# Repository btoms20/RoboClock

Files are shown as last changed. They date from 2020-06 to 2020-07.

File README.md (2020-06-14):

# RoboClock

Turning the [EEZYbotARM](https://www.thingiverse.com/thing:1015238) into a time telling machine! 

RoboClock_Timelapse

### Overview
This project attempts to use the [EEZYbotARM](https://www.thingiverse.com/thing:1015238) designed by [daGHIZmo](https://www.thingiverse.com/daGHIZmo) ([Original License](https://creativecommons.org/licenses/by-nc/4.0/legalcode)) to keep time by arranging a set of 3D printed numbers in the correct order.

The clock consists of three parts...
*  A Podium
    *  A stand that supports the digits used to tell the current time
*  An Inventory
    *  A chainlink / sprocket / tray system that stores all of the excess digits
    *  See Inventory.h for the arduino code
    *  See /Parts/Inventory for parts (stl) or [Thingiverse](https://www.thingiverse.com/thing:4457850/files)
*  The EEZYbot Robot Arm (see Arm.h)
    *  Responsible for moving the physical digits between the inventory and podium
    *  See Arm.h for the arduino code
    *  See [Thingiverse](https://www.thingiverse.com/thing:1015238) for parts
    *  With modified gripper assembly at 
       *  /Parts/GripperModified
       *  or [Thingiverse](https://www.thingiverse.com/thing:4457850)

Every 5 minutes the arm rearranges/replaces the numbers on the podium to reflect the current time. Depending on how many numbers need changing, the entire update cycle can last anywhere from 45 to 90 secs.

### How To
Check out the [instructables for a detailed guide](https://www.instructables.com/id/RoboClock/) to building your own
*  Download, Slice, Print and Assemble the [EEZYbotARM](https://www.thingiverse.com/thing:1015238) 
*  Download, Slice, Print and Assemble the [RoboClock](https://www.thingiverse.com/thing:4457850) parts
*  Pro Tip 💡: Before printing the entire 18 segment chain, print a few segments of the chain and adjust the height of Chain_Spacer.stl to make sure your chain has the desired tolerances. It should rotate freely with minimal lateral sag.
*  Mount parts to surface
*  Upload the meastro_settings.txt to the Micro Maestro using the Maestro software from Pololu
*  Tweak the sequences if needed to ensure the pre-programmed sequences move the to the correct locations
*  Wire up the electronics / circuit
*  Download the arduino sketch and dependencies using the IDE's library manager
*  Enter your wifi's credentials in arduino_secrets.h (if using the MKR1000 Wifi)
*  Compile & Upload the code to the arduino
*  Arrange the numbers on the chain in the anti-clockwise order (0,0,1,1,1,2,2,3,3,4,4,5,5,5,6,7,8,9)
*  Place the remaining zero on the last podium slot ( _ , _ , _ , 0 ) 
*  Plug in and watch it probably not work...
*  Tune the maestro sequences until things work 

### Arduino SketchBooks
*  [RoboClock_Seeeduino](https://gitlab.com/btoms20/robotclock/-/tree/master/clock_seeeduino) (Tested and working)
    *  Includes 3 custom libraries
        *  Clock.h
            *  Main orchestrator between Inventory and Arm
            *  Responsible for determining operations to acheive a certain clock state
            *  Repsonsible for the synchronous execution of those operations to achive the desired clock state
        * Arm.h
            *  Responsible for running pre-recorded subroutines on the Micro Maestro
        * Inventory.h
            *  Responsible for presenting requested digits (or empty slots) via the stepper motor diver.
            *  Responsible for maintaining an inventory state (what digit resides in each slot).
*  [RoboClock_MKR1000](https://gitlab.com/btoms20/robotclock/-/tree/master/clock_mkr1000) (Tested and working)
    *  Uses the Arduino MKR1000 Wifi
    *  The same Clock, Arm and Inventory libraries as above with the addition of networked time sync via NTP
    *  Also includes a few simple functions to convert UTC to your timezone (while protecting for daylight savings time when appropriate) (not fully tested)
    *  Two operation modes (set the ```Inventory.usingSensors``` bool flag appropriately)
        *  Using Hall Effect Chain Sensors (closes the inventory loop to create a much more robust inventory system)
        *  Not using Chain Sensors (the chain system may bind and cause the stepper motor to lose steps, at which point the system can't recover)

### Arduino Libraries / Dependencies
*  [PololuMaestro](https://github.com/pololu/maestro-arduino)
*  [CheapStepper](https://github.com/tyhenry/CheapStepper)
*  Seeeduino Specific
    *  [Time & TimeLib](https://github.com/PaulStoffregen)
*  MKR1000 Specific
    *  [RTCZero](https://github.com/arduino-libraries/RTCZero/blob/master/src/RTCZero.h)

### Hardware ( ~150 USD if you need to purchase everything listed )
*  Pololu Servo Controller ([Micro Maestro](https://www.pololu.com/product/1350)) (requires 5v serial)
*  4x MG90S Servos
*  28BYJ-48 5V DC Stepper Motor 
*  ULN2003A Stepper Driver
*  MKR1000 or Seeeduino rev2.21 (used for its 5v gpio pins)
*  Voltage Level Shifter (if using 3.3v board like the Arduino MKR1000 Wifi)
*  5v ~3 Amp Power Supply
*  608ZZ Bearing
*  Assorted M3-M5 Nuts and Bolts (lock nuts recommended)
*  Jumper Wires and Breadboard
*  3x1mm Magnets
*  A3144 Hall Effect Sensors (optional but recommended)

### Tools
*  3D Printer
*  Windows Comp with USB for Pololu Meastro Software 
*  Arduino IDE
*  M3-M5 Allen Keys
*  Pliers
*  Wood Screws and Screw Driver
*  A surface to mount everything to (a recycled bookshelf works well)
*  Superglue
If using the chain sensor
*  Soldering Iron
*  2x Capacitors (0.1 uF)
*  2x Resistors (10k Ohms)

### Electronics / Circuit Diagram
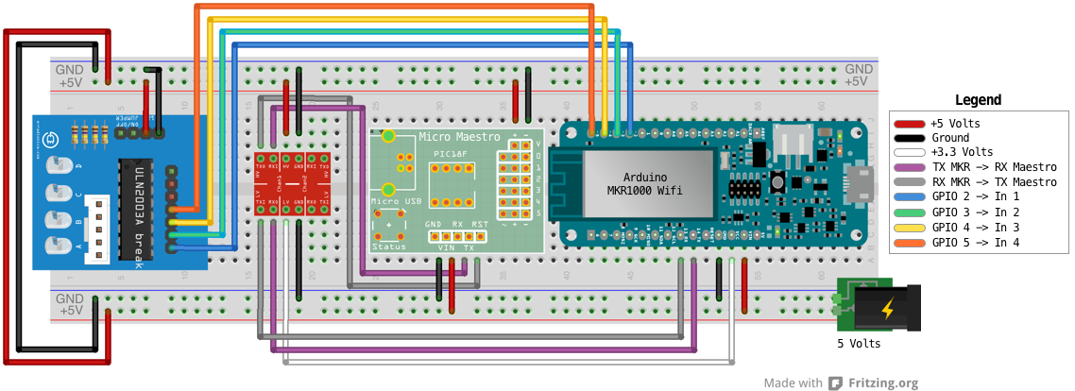
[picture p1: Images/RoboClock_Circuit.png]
RoboClock_Circuit


### Variants
* [x]  Seeeduino Controller (done)
    *  Pros:
        *  Makes development simple. Has 5v serial that makes interfacing with the micro maestro easy.
    *  Downsides 
        * No network for time sync / management 
        * Limited RAM (we're currently at ~85% memory and getting warnings on the Arduino IDE)
* [x]  Arduino MKR1000 (~~waiting for logic level shifter~~)
    *  Pros:
        *  Wifi built in for time sync / management
        *  Faster & more RAM
    *  Cons:
        *  3.3v architecture requires the use of a 3.3v <-> 5v Logic Level Shifter for communication with the Micro Maestro
* [ ]  TODO: Raspberry Pi Zero W (not started, 3.3v gpio as well)

### Notes & References
*  Arduino 
    * [Writing a Library](https://www.arduino.cc/en/Hacking/LibraryTutorial)  
*  MKR1000
    *  [Additional Serial Ports - Example Code](https://github.com/guywithaview/Arduino-Test/blob/master/sercom/sercom.ino)
    *  [Additional Serial Ports - Forum](https://forum.arduino.cc/index.php?topic=393296.0)
    *  [WiFiRTC Example](https://www.arduino.cc/en/Tutorial/WiFiRTC)
*  [Micro Maestro Documentation](https://www.pololu.com/product/1350)
*  [Unipolar -> Bipolar 28BYJ Conversion](https://coeleveld.com/wp-content/uploads/2016/10/Modifying-a-28BYJ-48-step-motor-from-unipolar-to-bipolar.pdf)
*  Raspberry Pi
    *  [28BYJ Stepper Motor & ULN2003 Driver](https://learn.adafruit.com/adafruits-raspberry-pi-lesson-10-stepper-motors/overview)  

### 3D Printed Parts
*  [EEZYbotARM MRK 1](https://www.thingiverse.com/thing:1015238) designed by [daGHIZmo](https://www.thingiverse.com/daGHIZmo) ([Original License](https://creativecommons.org/licenses/by-nc/4.0/legalcode))
*  [RoboClock](https://www.thingiverse.com/thing:4457850)

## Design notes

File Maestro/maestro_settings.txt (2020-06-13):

<!--Pololu Maestro servo controller settings file, http://www.pololu.com/catalog/product/1350-->
<UscSettings version="1">
  <NeverSuspend>false</NeverSuspend>
  <SerialMode>UART_FIXED_BAUD_RATE</SerialMode>
  <FixedBaudRate>9600</FixedBaudRate>
  <SerialTimeout>0</SerialTimeout>
  <EnableCrc>false</EnableCrc>
  <SerialDeviceNumber>12</SerialDeviceNumber>
  <SerialMiniSscOffset>0</SerialMiniSscOffset>
  <Channels ServosAvailable="6" ServoPeriod="156">
    <!--Period = 19.968 ms-->
    <!--Channel 0-->
    <Channel name="" mode="Servo" min="1792" max="10432" homemode="Off" home="1792" speed="0" acceleration="4" neutral="6000" range="1905" />
    <!--Channel 1-->
    <Channel name="" mode="Servo" min="3968" max="8000" homemode="Off" home="3968" speed="0" acceleration="0" neutral="6000" range="1905" />
    <!--Channel 2-->
    <Channel name="" mode="Servo" min="4032" max="9216" homemode="Off" home="4032" speed="0" acceleration="8" neutral="6000" range="1905" />
    <!--Channel 3-->
    <Channel name="" mode="Servo" min="3584" max="8000" homemode="Off" home="3584" speed="0" acceleration="8" neutral="6000" range="1905" />
    <!--Channel 4-->
    <Channel name="" mode="Servo" min="1600" max="9984" homemode="Off" home="1600" speed="0" acceleration="0" neutral="6000" range="1905" />
    <!--Channel 5-->
    <Channel name="" mode="Servo" min="5824" max="9216" homemode="Off" home="5824" speed="0" acceleration="10" neutral="6400" range="1905" />
  </Channels>
  <Sequences>
    <Sequence name="ActiveHome">
      <Frame name="ActiveHome" duration="2000">5920 0 6800 4000 0 5824</Frame>
    </Sequence>
    <Sequence name="Pick0">
      <Frame name="Home" duration="1500">5920 0 6800 4000 0 5824</Frame>
      <Frame name="Frame 0" duration="2500">9800 0 6800 4000 0 8000</Frame>
      <Frame name="Frame 1" duration="1000">9800 0 6160 4600 0 8000</Frame>
      <Frame name="Frame 2" duration="1500">9800 0 4800 5600 0 8000</Frame>
      <Frame name="Frame 3" duration="1000">9800 0 4800 5600 0 5824</Frame>
      <Frame name="Frame 4" duration="200">9600 0 4800 5600 0 5824</Frame>
      <Frame name="Frame 5" duration="1500">9600 0 6800 4000 0 5824</Frame>
      <Frame name="Home" duration="1500">5920 0 6800 4000 0 5824</Frame>
    </Sequence>
    <Sequence name="Pick1">
      <Frame name="Home" duration="1500">5920 0 6800 4000 0 5824</Frame>
      <Frame name="Frame 0" duration="2500">9800 0 6800 4000 0 8000</Frame>
      <Frame name="Frame 1" duration="1000">9800 0 6160 5280 0 8000</Frame>
      <Frame name="Frame 2" duration="1000">9800 0 5200 6000 0 8000</Frame>
      <Frame name="Frame 3" duration="1000">9800 0 5200 6000 0 5824</Frame>
      <Frame name="Frame 4" duration="200">9600 0 5200 6000 0 5824</Frame>
      <Frame name="Frame 5" duration="1500">9600 0 6160 5280 0 5824</Frame>
      <Frame name="Frame 6" duration="1500">9600 0 6800 4000 0 5824</Frame>
      <Frame name="Home" duration="1500">5920 0 6800 4000 0 5824</Frame>
    </Sequence>
    <Sequence name="Pick2">
      <Frame name="Home" duration="1500">5920 0 6800 4000 0 5824</Frame>
      <Frame name="Frame 0" duration="2500">9800 0 6800 4000 0 8000</Frame>
      <Frame name="Frame 1" duration="1000">9800 0 6800 5880 0 8000</Frame>
      <Frame name="Frame 2" duration="1000">9800 0 5720 6520 0 8000</Frame>
      <Frame name="Frame 3" duration="1000">9800 0 5720 6520 0 5824</Frame>
      <Frame name="Frame 4" duration="200">9600 0 5720 6520 0 5824</Frame>
      <Frame name="Frame 5" duration="1500">9600 0 6800 5880 0 5824</Frame>
      <Frame name="Frame 6" duration="1500">9600 0 6800 4000 0 5824</Frame>
      <Frame name="Home" duration="1500">5920 0 6800 4000 0 5824</Frame>
    </Sequence>
    <Sequence name="Pick3">
      <Frame name="Home" duration="1500">5920 0 6800 4000 0 5824</Frame>
      <Frame name="Frame 0" duration="2500">9800 0 6800 4000 0 8000</Frame>
      <Frame name="Frame 1" duration="1000">9800 0 7200 6800 0 8000</Frame>
      <Frame name="Frame 2" duration="1000">9800 0 6320 7120 0 8000</Frame>
      <Frame name="Frame 3" duration="1000">9800 0 6320 7120 0 5824</Frame>
      <Frame name="Frame 4" duration="200">9680 0 6320 7120 0 5824</Frame>
      <Frame name="Frame 5" duration="1500">9680 0 7600 6800 0 5824</Frame>
      <Frame name="Frame 6" duration="1500">9680 0 6800 4000 0 5824</Frame>
      <Frame name="Home" duration="1500">5920 0 6800 4000 0 5824</Frame>
    </Sequence>
    <Sequence name="PickTray">
      <Frame name="Home" duration="1500">5920 0 6800 4000 0 5824</Frame>
      <Frame name="Frame 0" duration="2500">2200 0 6800 4000 0 8000</Frame>
      <Frame name="Frame 2" duration="1500">2200 0 5400 5400 0 8000</Frame>
      <Frame name="Frame 3" duration="1000">2200 0 5400 5400 0 5824</Frame>
      <Frame name="Frame 5" duration="1">2600 0 5400 5400 0 5824</Frame>
      <Frame name="Frame 4" duration="2000">2600 0 6800 4000 0 5824</Frame>
      <Frame name="Home" duration="1500">5920 0 6800 4000 0 5824</Frame>
    </Sequence>
    <Sequence name="Place0">
      <Frame name="Home" duration="1500">5920 0 6800 4000 0 5824</Frame>
      <Frame name="Frame 0" duration="2500">9800 0 6800 4000 0 5824</Frame>
      <Frame name="Frame 1" duration="1000">9800 0 6160 4600 0 5824</Frame>
      <Frame name="Frame 2" duration="1500">9800 0 4800 5600 0 5824</Frame>
      <Frame name="Frame 3" duration="750">9800 0 4800 5600 0 8000</Frame>
      <Frame name="Frame 4" duration="1500">9800 0 6800 4000 0 8000</Frame>
      <Frame name="Frame 5" duration="750">9800 0 6800 4000 0 6000</Frame>
      <Frame name="Home" duration="1500">5920 0 6800 4000 0 5824</Frame>
    </Sequence>
    <Sequence name="Place1">
      <Frame name="Home" duration="1500">5920 0 6800 4000 0 5824</Frame>
      <Frame name="Frame 0" duration="2500">9840 0 6800 4000 0 5824</Frame>
      <Frame name="Frame 1" duration="1500">9840 0 6400 5280 0 5824</Frame>
      <Frame name="Frame 2" duration="1500">9840 0 5200 6000 0 5824</Frame>
      <Frame name="Frame 3" duration="750">9840 0 5200 6000 0 8000</Frame>
      <Frame name="Frame 4" duration="1500">9840 0 6160 5280 0 8000</Frame>
      <Frame name="Frame 5" duration="1000">9840 0 6800 4000 0 6000</Frame>
      <Frame name="Home" duration="1500">5920 0 6800 4000 0 5824</Frame>
    </Sequence>
    <Sequence name="Place2">
      <Frame name="Home" duration="1500">5920 0 6800 4000 0 5824</Frame>
      <Frame name="Frame 0" duration="2500">9880 0 6800 4000 0 5824</Frame>
      <Frame name="Frame 1" duration="1000">9880 0 6800 5880 0 5824</Frame>
      <Frame name="Frame 6" duration="1000">9880 0 6000 6120 0 5824</Frame>
      <Frame name="Frame 2" duration="1000">9880 0 5720 6520 0 5824</Frame>
      <Frame name="Frame 3" duration="750">9880 0 5720 6520 0 8000</Frame>
      <Frame name="Frame 4" duration="1000">9880 0 6800 5880 0 8000</Frame>
      <Frame name="Frame 5" duration="1000">9880 0 6800 4000 0 6000</Frame>
      <Frame name="Home" duration="1500">5920 0 6800 4000 0 5824</Frame>
    </Sequence>
    <Sequence name="Place3">
      <Frame name="Home" duration="1500">5920 0 6800 4000 0 5824</Frame>
      <Frame name="Frame 0" duration="2500">9880 0 6800 4000 0 5824</Frame>
      <Frame name="Frame 1" duration="1500">9880 0 7200 6800 0 5824</Frame>
      <Frame name="Frame 2" duration="1000">9880 0 6320 7040 0 5824</Frame>
      <Frame name="Frame 3" duration="750">9880 0 6600 7200 0 8000</Frame>
      <Frame name="Frame 4" duration="1000">9880 0 7200 6800 0 8000</Frame>
      <Frame name="Frame 5" duration="2000">9880 0 6800 4000 0 6000</Frame>
      <Frame name="Home" duration="1500">5920 0 6800 4000 0 5824</Frame>
    </Sequence>
    <Sequence name="PlaceTray">
      <Frame name="Home" duration="1500">5920 0 6800 4000 0 5824</Frame>
      <Frame name="Frame 0" duration="2500">2200 0 6800 4000 0 5824</Frame>
      <Frame name="Hover" duration="1500">2200 0 5800 5000 0 5824</Frame>
      <Frame name="Place" duration="1500">2200 0 5200 5400 0 6400</Frame>
      <Frame name="Frame 2" duration="750">2200 0 5200 5400 0 8000</Frame>
      <Frame name="Frame 3" duration="1500">2200 0 6800 4000 0 8000</Frame>
      <Frame name="Frame 4" duration="750">2200 0 6800 4000 0 6000</Frame>
      <Frame name="Home" duration="1500">5920 0 6800 4000 0 5824</Frame>
    </Sequence>
  </Sequences>
  <Script ScriptDone="true">begin
repeat

### Sequence subroutines: ###

# ActiveHome
sub ActiveHome
  2000 5920 0 6800 4000 0 6000 frame_0..5 # ActiveHome
  return
# Pick0
sub Pick0
  2500 9800 0 6800 4000 0 8000 frame_0..5 # Frame 0
  1000 6160 4600 frame_2_3 # Frame 1
  1500 4800 5600 frame_2_3 # Frame 2
  1000 5824 frame_5 # Frame 3
  200 9600 frame_0 # Frame 4
  1500 6800 4000 frame_2_3 # Frame 5
  return
# Pick1
sub Pick1
  2500 9800 0 6800 4000 0 8000 frame_0..5 # Frame 0
  1000 6160 5280 frame_2_3 # Frame 1
  1000 5200 6000 frame_2_3 # Frame 2
  1000 5824 frame_5 # Frame 3
  200 9600 frame_0 # Frame 4
  1500 6160 5280 frame_2_3 # Frame 5
  1500 6800 4000 frame_2_3 # Frame 6
  return
# Pick2
sub Pick2
  2500 9800 0 6800 4000 0 8000 frame_0..5 # Frame 0
  1000 5880 frame_3 # Frame 1
  1000 5720 6520 frame_2_3 # Frame 2
  1000 5824 frame_5 # Frame 3
  200 9600 frame_0 # Frame 4
  1500 6800 5880 frame_2_3 # Frame 5
  1500 4000 frame_3 # Frame 6
  return
# Pick3
sub Pick3
  2500 9800 0 6800 4000 0 8000 frame_0..5 # Frame 0
  1000 7200 6800 frame_2_3 # Frame 1
  1000 6320 7120 frame_2_3 # Frame 2
  1000 5824 frame_5 # Frame 3
  200 9680 frame_0 # Frame 4
  1500 7600 6800 frame_2_3 # Frame 5
  1500 6800 4000 frame_2_3 # Frame 6
  return
# PickTray
sub PickTray
  2500 2200 0 6800 4000 0 8000 frame_0..5 # Frame 0
  1500 5400 5400 frame_2_3 # Frame 2
  1000 5824 frame_5 # Frame 3
  1 2600 frame_0 # Frame 5
  2000 6800 4000 frame_2_3 # Frame 4
  return
# Place0
sub Place0
  2500 9800 0 6800 4000 0 5824 frame_0..5 # Frame 0
  1000 6160 4600 frame_2_3 # Frame 1
  1500 4800 5600 frame_2_3 # Frame 2
  750 8000 frame_5 # Frame 3
  1500 6800 4000 frame_2_3 # Frame 4
  750 6000 frame_5 # Frame 5
  return
# Place1
sub Place1
  2500 9840 0 6800 4000 0 5824 frame_0..5 # Frame 0
  1500 6400 5280 frame_2_3 # Frame 1
  1500 5200 6000 frame_2_3 # Frame 2
  750 8000 frame_5 # Frame 3
  1500 6160 5280 frame_2_3 # Frame 4
  1000 6800 4000 6000 frame_2_3_5 # Frame 5
  return
# Place2
sub Place2
  2500 9880 0 6800 4000 0 5824 frame_0..5 # Frame 0
  1000 5880 frame_3 # Frame 1
  1000 6000 6120 frame_2_3 # Frame 6
  1000 5720 6520 frame_2_3 # Frame 2
  750 8000 frame_5 # Frame 3
  1000 6800 5880 frame_2_3 # Frame 4
  1000 4000 6000 frame_3_5 # Frame 5
  return
# Place3
sub Place3
  2500 9880 0 6800 4000 0 5824 frame_0..5 # Frame 0
  1500 7200 6800 frame_2_3 # Frame 1
  1000 6320 7040 frame_2_3 # Frame 2
  750 6600 7200 8000 frame_2_3_5 # Frame 3
  1000 7200 6800 frame_2_3 # Frame 4
  2000 6800 4000 6000 frame_2_3_5 # Frame 5
  return
# PlaceTray
sub PlaceTray
  2500 2200 0 6800 4000 0 5824 frame_0..5 # Frame 0
  1500 5800 5000 frame_2_3 # Hover
  1500 5200 5400 6400 frame_2_3_5 # Place
  750 8000 frame_5 # Frame 2
  1500 6800 4000 frame_2_3 # Frame 3
  750 6000 frame_5 # Frame 4
  return

sub frame_0..5
  5 servo
  4 servo
  3 servo
  2 servo
  1 servo
  0 servo
  delay
  return

sub frame_2_3
  3 servo
  2 servo
  delay
  return

sub frame_5
  5 servo
  delay
  return

sub frame_0
  0 servo
  delay
  return

sub frame_3
  3 servo
  delay
  return

sub frame_2_3_5
  5 servo
  3 servo
  2 servo
  delay
  return

sub frame_3_5
  5 servo
  3 servo
  delay
  return
</Script>
</UscSettings>

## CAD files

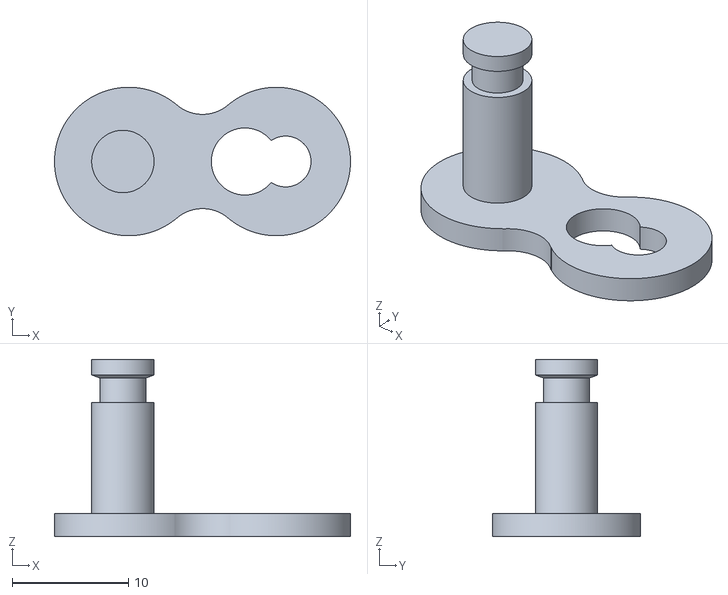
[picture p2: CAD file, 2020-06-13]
Parts/Inventory/Chain/Main_Bracket.stl
25.5 x 12.8 x 15.2

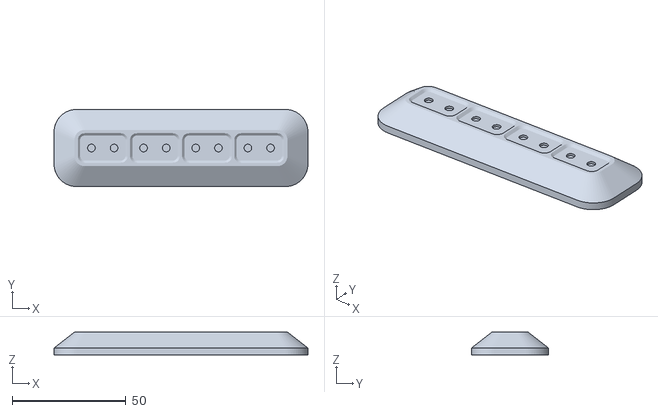
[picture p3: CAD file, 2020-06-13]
Parts/Clock_Podium.stl
111.9 x 34.0 x 10.0

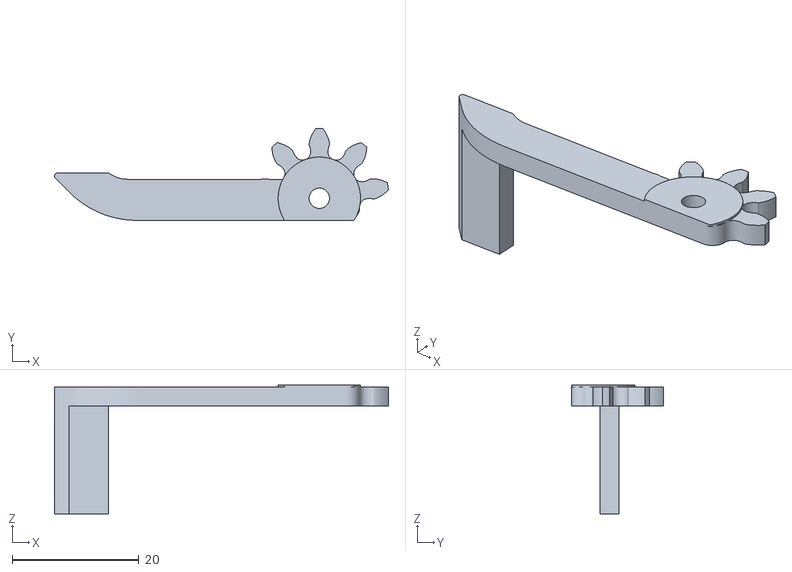
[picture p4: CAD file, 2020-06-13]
Parts/GripperModified/EBA_Left_Finger_Extended.stl
52.7 x 14.5 x 20.3

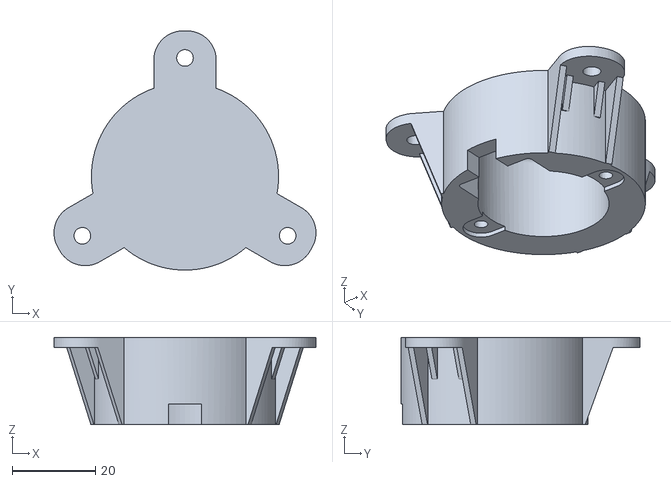
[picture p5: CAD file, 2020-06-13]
Parts/Inventory/28BYJ_Motor_Mount.stl
63.0 x 57.5 x 21.0

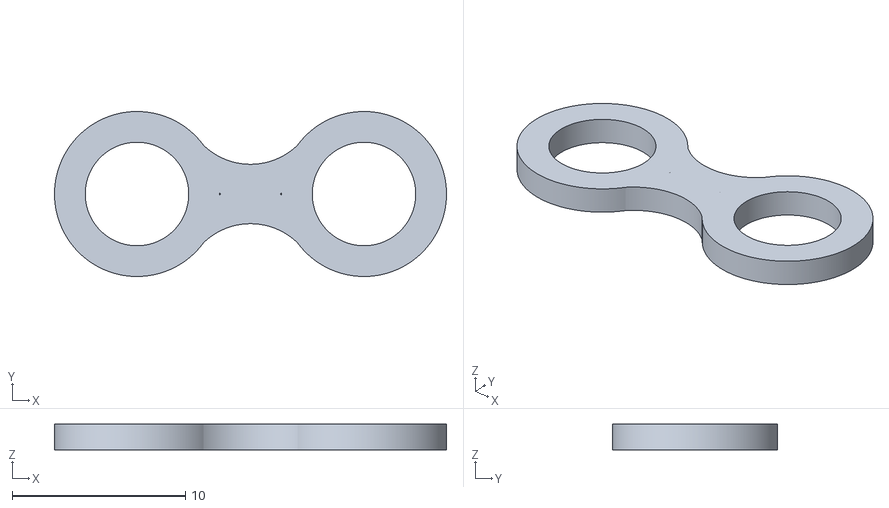
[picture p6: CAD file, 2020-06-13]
Parts/Inventory/Chain/Connector_Bracket.stl
22.6 x 9.52 x 1.50

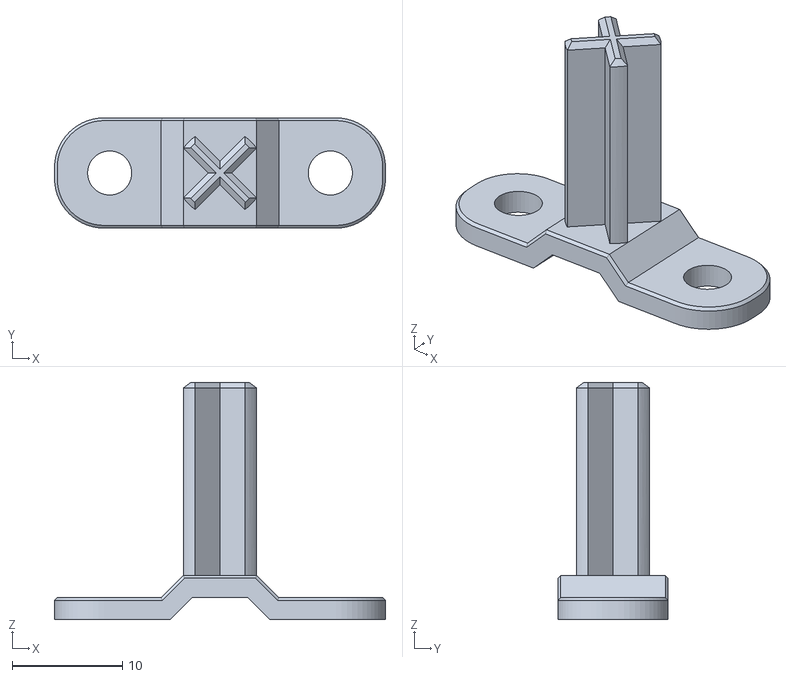
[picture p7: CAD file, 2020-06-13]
Parts/Inventory/Guides/Guide_Rail_Tower_19p5_Bridged.stl
30.0 x 10.0 x 21.5

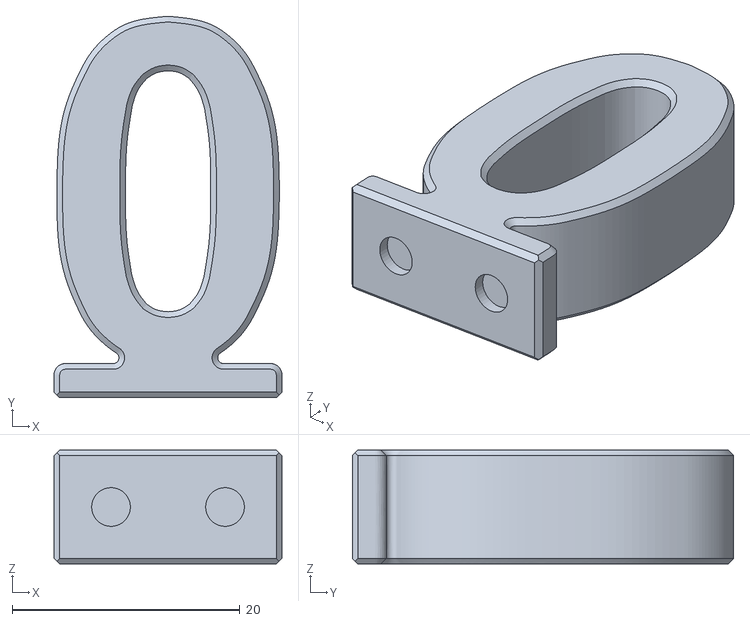
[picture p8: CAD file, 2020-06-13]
Parts/Numbers/Number(Zero).stl
20.0 x 33.5 x 10.0

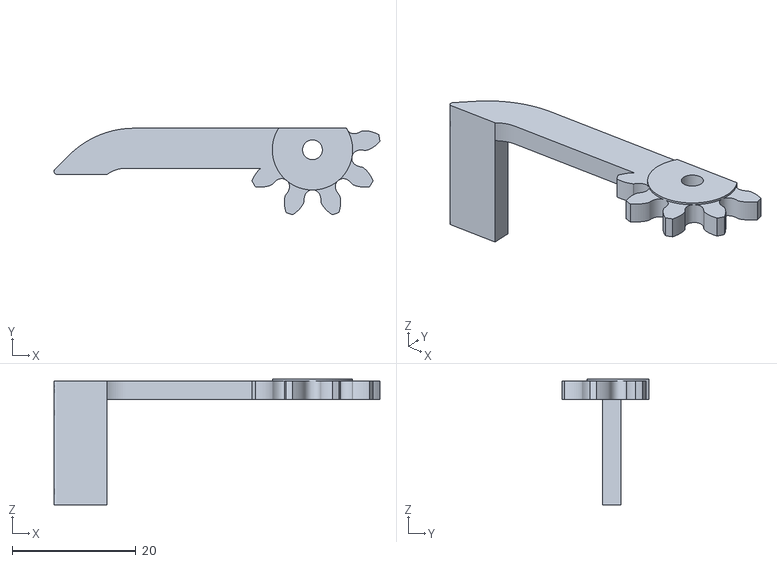
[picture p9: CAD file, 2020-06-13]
Parts/GripperModified/EBA_Right_Finger_Extended.stl
52.7 x 14.0 x 20.3

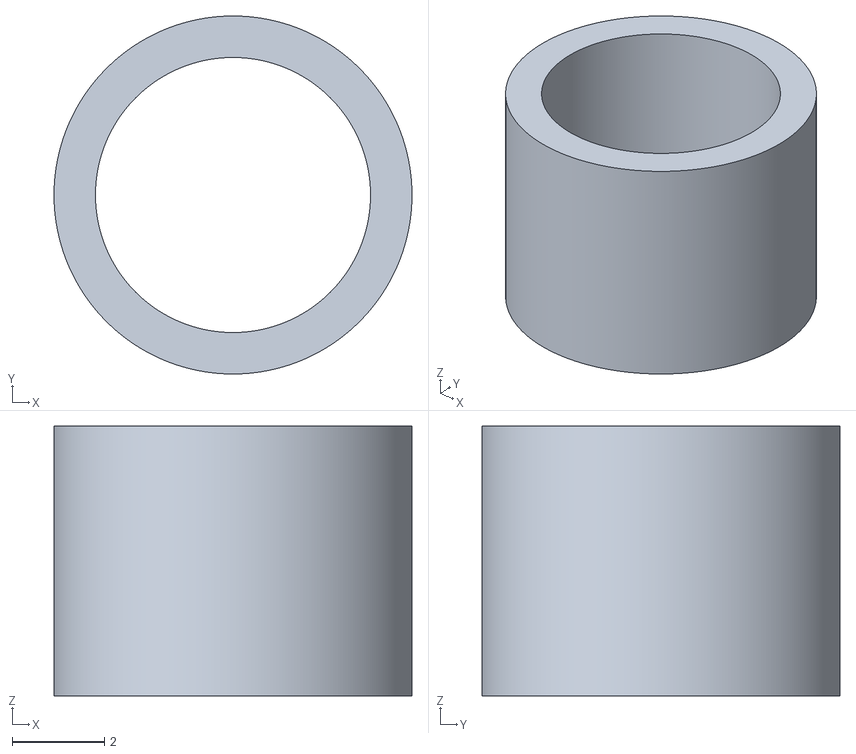
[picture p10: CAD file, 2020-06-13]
Parts/Inventory/Chain/Chain_Spacer.stl
7.77 x 7.77 x 5.85

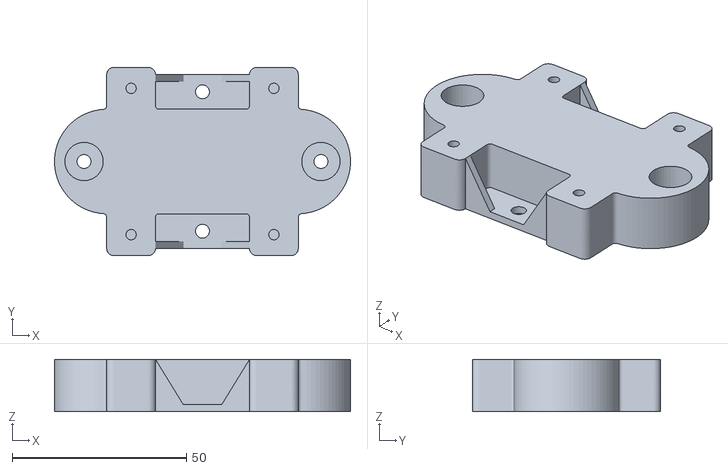
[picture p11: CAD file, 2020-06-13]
Parts/Inventory/Chain_Tensioner_Standoff.stl
85.0 x 54.0 x 15.0

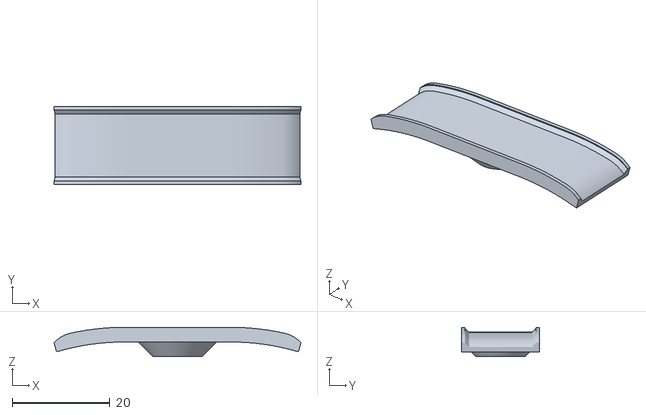
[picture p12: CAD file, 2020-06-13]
Parts/Inventory/Guides/Guide_Rail_Top.stl
50.4 x 16.0 x 6.00

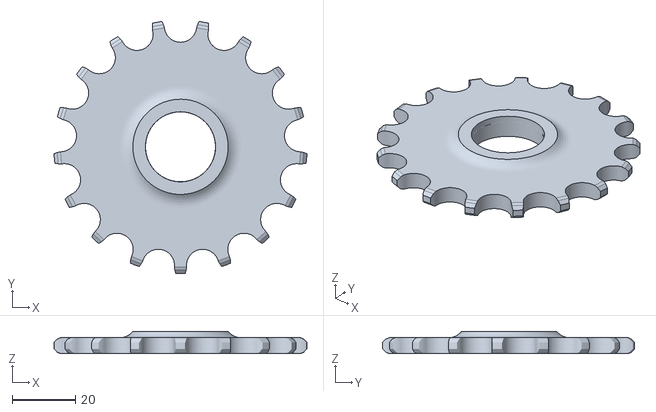
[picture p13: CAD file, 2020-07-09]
Parts/Inventory/Sprockets/Clock_Sprocket_17.stl
79.7 x 79.4 x 7.00

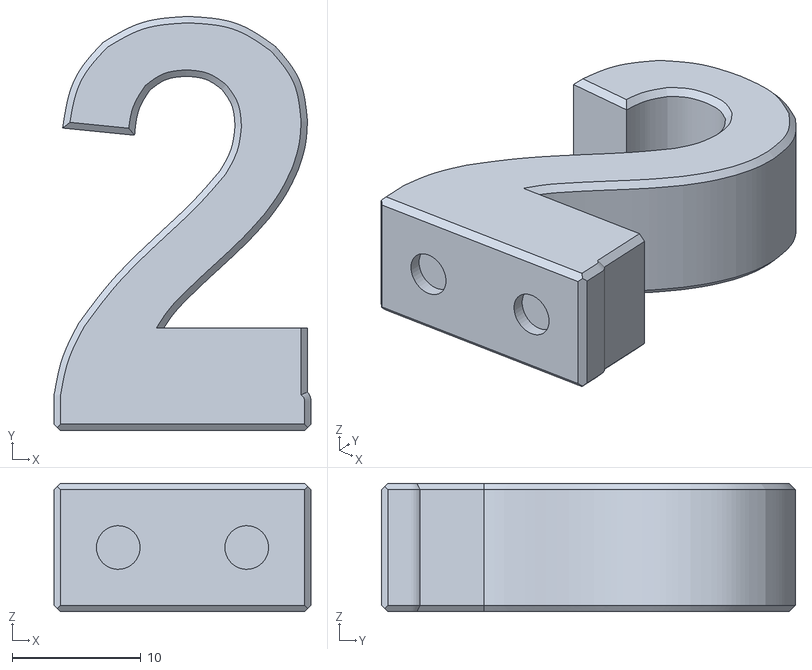
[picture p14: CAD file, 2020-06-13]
Parts/Numbers/Number(Two).stl
20.0 x 32.2 x 10.0

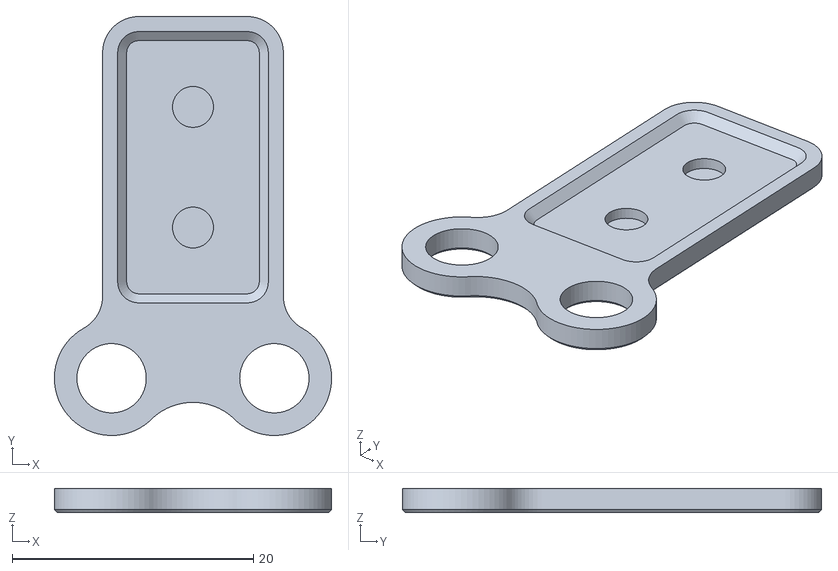
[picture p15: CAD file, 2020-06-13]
Parts/Inventory/Chain/Chain_Link_Tray.stl
23.0 x 34.7 x 2.00

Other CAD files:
Parts/Inventory/M5_Bearing_Sleeve.stl
Parts/Numbers/Number(Six).stl
Parts/Inventory/Chain_Sensor_Housing.stl
Parts/Numbers/Number(Five).stl
Parts/Inventory/Chain_Tensioner.stl
Parts/Inventory/Sprockets/Clock_Sprocket_12_Bolt.stl
Parts/Numbers/Number(Eight).stl
Parts/Numbers/Number(Four).stl
Parts/Numbers/Number(Nine).stl
Parts/Numbers/Number(One).stl
Parts/Numbers/Number(Seven).stl
Parts/Numbers/Number(Three).stl

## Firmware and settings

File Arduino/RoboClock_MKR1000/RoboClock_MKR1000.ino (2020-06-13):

#include "Clock.h"
#include "WifiTime.h"

Clock myClock;
WifiTime wt;
int counter = 0;
bool alarmSet = false;

void setup() {  
  Serial.begin(9600);

  delay(500);

  Serial.println("Initializing Wifi and fetching time...");

  //Init Wifi and Sync RTC Time
  wt.initialize();
  wt.timezoneOffset = -8; //UTC Timezone Offset (-8 = PST, -5 = EST, +2 = Paris, etc) 

  //Init clock state (podium numbers)
  myClock.inventory.usingSensors = true; //Set this to 'true' if you're using the hall effect chain sensors
  myClock.initClockState(-1, -1, -1, 0); //-1 == empty slot

  delay(1000);

  Serial.println("Clock Ready...");

  //Update the clock to the nearest incement of 5
  int first[] = {-1, -1};
  nextIncrementOf(5, first);
  adjustForTimezone(first);
  myClock.setTime(toTwelve(first[0]), first[1]);
  
  Serial.print("Current Time ");
  Serial.print(wt.currentHour());
  Serial.print(":");
  Serial.print(wt.currentMinute());
  Serial.println(" Timezone");

  Serial.print("Clock Set for ");
  Serial.print(first[0]);
  Serial.print(":");
  Serial.print(first[1]);
  Serial.println(" Timezone");
}


void loop() {
  myClock.run();

  if (alarmSet == false) { 
    setNextAlarm();
  }
}

//Grabs the current time / date and sets an alarm to trigger the next clock update (next 5 minute interval)
void setNextAlarm() {
  int next[] = {-1, -1};
  nextIncrementOf(5, next);
  wt.rtc.setAlarmTime(next[0], next[1], 0);
  wt.rtc.enableAlarm(wt.rtc.MATCH_HHMMSS);
  wt.rtc.attachInterrupt(updateClockTime);

  alarmSet = true;
  Serial.print("Alarm Set for ");
  Serial.print(next[0]);
  Serial.print(":");
  Serial.print(next[1]);
  Serial.println(" UTC");
}

//Returns the next increment of UTC time...
//Works in 24 Hour Format
void nextIncrementOf(int n, int *arr) {
  //Get the current time
  int minutes = wt.rtc.getMinutes() + 1;
  int hours = wt.rtc.getHours();
  if (minutes >= (59 - n)) {
    hours++;
    minutes = 0;
  }
  minutes = (minutes + (n-1)) / n * n; //Round up to increment of n
  if (hours >= 24) {
    hours = 0;
  }
  arr[0] = hours;
  arr[1] = minutes;
}

//Works in 24 Hour Format
void adjustForTimezone(int *arr) {
  if (arr[0] == -1 || arr[1] == -1) { return; }
  arr[0] = wt.currentHour();
  if (arr[1] == 0) {
    arr[0] += 1;
    if (arr[0] >= 24) {
      arr[0] = 0;
    }
  }
}

//Converts a 24 Hour Format digit into 12 Hour Format...
int toTwelve(int hour) {
  int h = hour % 12;
  if (h == 0) { return 12; }
  return h;
}

void updateClockTime() {
  //Set Next Alarm...
  alarmSet = false;
  
  //Update Clock...
  Serial.println("Updating Clock...");
  wt.printDate();
  Serial.print(wt.currentHour());
  Serial.print(":");
  Serial.print(wt.currentMinute());
  Serial.println(" Timezone");

  myClock.setTime(wt.currentHour(), wt.currentMinute());
}

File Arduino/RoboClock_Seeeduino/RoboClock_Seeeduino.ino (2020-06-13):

#include <Time.h>
#include <TimeLib.h>

#include "Clock.h"

Clock myClock;
int counter = 0;

//*** Before Uploading ****
//1) Clock Podium should be empty except for a single zero in the last slot
//2) Inventory numbers should be in the following counter clockwise order 
//   (0,0,1,1,1,2,2,3,3,4,4,5,5,5,6,7,8,9) with the first zero placed at the active tray location 
//3) Software serial comms through pins D5 & D6 (this can be changed in Clock.cpp initializer)
//4) 28BYJ motor control via ULN2003 through default pins D8,D9,D10 & D11 (this can be changed in Inventory.cpp initializer) 

void setup() {
  // Manually set the current time (hr,min,sec,day,mnth,yr)
  setTime(13, 10, 20, 8, 4, 20);
  
  Serial.begin(9600);

  delay(100);
  
  Serial.println("Clock Test Ready...");

  //Let the clock know the initial podium state (-1 == empty slot)
  myClock.initClockState(-1, -1, -1, 0);

  delay(1000);
}

void loop() {
  counter++;

  if (counter % 5000 == 0) { //Only check the time once every 5 seconds...
    counter = 0;
    time_t t = now();
    if (minute(t) % 10 == 4) { //begin update
      int hour12 = hour(t) % 12;
      if (hour12 == 0) { hour12 = 12; }
      Serial.print("Setting the time to ");
      Serial.print(hour12);
      Serial.print(":");
      Serial.println(minute(t) + 1);
      myClock.setTime(hour12, minute(t)+1);
    } else if (minute(t) % 10 == 9) { //begin update
      int hour12 = hour(t);
      if (minute(t) == 59) {
        //Next Hour...
        hour12 += 1;
      }
      hour12 = hour12 % 12;
      if (hour12 == 0) { hour12 = 12; }
      int minutes = (minute(t) + 1) % 60;
      Serial.print("Setting the time to ");
      Serial.print(hour12);
      Serial.print(":");
      Serial.println(minutes);
      myClock.setTime(hour12, minutes);
    }
  }
  
  myClock.run();
}

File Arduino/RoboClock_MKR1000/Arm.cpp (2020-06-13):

#include "Arduino.h"
#include "Arm.h"

//Micro Maestro Library
#include "PololuMaestro.h"

#define _maestroSerial SERIAL_PORT_HARDWARE_OPEN
Arm::Arm() : _maestro(_maestroSerial) {
  _isMoving = false;
  _currentSubroutine = -1;
}

void Arm::initialize() {
  //Start comms with the maestro
  _maestroSerial.begin(9600);

  delay(100);

  //Configure Servo Acceleration
  _maestro.setAcceleration(0, 4);
  _maestro.setAcceleration(2, 8);
  _maestro.setAcceleration(3, 8);
  _maestro.setAcceleration(5, 10);

  Serial.println("ARM::Initialized");
}

//Called every loop cycle (should be cheap)
//getScriptStatus == 1 when the script has finished
//getScriptStatus == 0 when the script is running
void Arm::updateSelf() {
  if (_isMoving && (_maestro.getScriptStatus() == 1)) {
    //We just finished a subroutine
    Serial.print("Arm::Finished Subroutine ");
    Serial.println(_currentSubroutine);
    _currentSubroutine = -1;
    _isMoving = false;
    _updateInterval = 0;
  }
}

//Called every loop cycle (should be cheap)
bool Arm::isWorking() {
  return _isMoving;
}

bool Arm::startSequence(int subroutine) {
  if (_maestro.getScriptStatus() == 1) {
    //We're ready to start a new sequence
    Serial.print("Arm::Running SubRoutine ");
    Serial.println(subroutine);
    
    _maestro.restartScript(subroutine);
    _currentSubroutine = subroutine;
    _isMoving = true;
    return true;
  } else {
    return false;
  }
}

void Arm::stopSequence() {
  if (_maestro.getScriptStatus() == 0) {
    Serial.print("Arm::Stopping SubRoutine ");
    Serial.println(_currentSubroutine);
    _maestro.stopScript();
    _currentSubroutine = -1;
    _isMoving = false;
  }
}

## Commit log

2020-06-13 Added timelapse gif and circuit diagram to README
2020-07-09 Fixed Sprocket STL scale
    [Clock_Sprocket_12_Bolt.stl, Clock_Sprocket_17.stl]
